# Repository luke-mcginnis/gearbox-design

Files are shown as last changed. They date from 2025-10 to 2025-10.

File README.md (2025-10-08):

# Gearbox Design Project

This was my final project for ME 330: Machine Design. The project goal was to design a three-stage gearbox using machine design principles including fatigue and failure analysis, material selection, bearing selection, and the AGMA design process. The end deliverables for this project were a [final report](/report.pdf) and gearbox powertrain CAD.

## [View final report](/report.pdf)
## [View final CAD](https://grabcad.com/library/three-stage-gearbox-2)

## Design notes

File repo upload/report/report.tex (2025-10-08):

\documentclass[titlepage]{article} % letter paper is implicit

\usepackage{siunitx} % for units
\usepackage{mathtools} % for amsmath
\usepackage{booktabs} % for better-looking tables
\usepackage{threeparttable} % for notes in tables
\usepackage[title]{appendix}
\usepackage{listings} % for source code
\usepackage{courier}
\usepackage[x11names]{xcolor} % for source code colors
\usepackage[moderate, % package to fit more text on a page, set moderate spacing
            mathspacing=normal, % keep horizontal spacing in math
            mathdisplays=normal, % keep vertical spacing around math
            leading=normal, % keep line spacing normal
            margins=tight, % allow custom margins (below)
            indent=normal,  % indent paragraphs normally
            marginwidth=1in]{savetrees} % set margin to 1in
\usepackage{biblatex} % For bibliography
\usepackage{amssymb} % For lists?
\usepackage{enumitem} % For lists?
\usepackage{tikz}  % FBDs with Plots
\usepackage{pgf} % Math printings
\usepackage{subcaption} % side by side figures
\usepackage{graphicx} % pictures
\usepackage{pdfpages} % drawings
% \setlength{\footskip}{30pt}

\sisetup{
    group-digits=integer,
    group-minimum-digits={3},
    group-separator={,},
    uncertainty-mode = separate,
    separate-uncertainty-units = single
}

\definecolor{codebackcolor}{rgb}{0.95,0.95,0.92}

\lstdefinestyle{myStyle}{
    backgroundcolor=\color{codebackcolor},   
    numberstyle=\tiny\color{gray},
    basicstyle=\ttfamily\footnotesize,
    identifierstyle=\color{Blue3},
    commentstyle=\color{SpringGreen4},
    keywordstyle=\color{Magenta3},
    stringstyle=\color{DarkOrange2},
    breakatwhitespace=false,         
    breaklines=true,                 
    keepspaces=true,                 
    numbers=left,       
    numbersep=5pt,                  
    showspaces=false,                
    showstringspaces=false,
    showtabs=false,                  
    tabsize=2,
}

\addbibresource{references.bib} % Import the bibliography file

\usetikzlibrary{backgrounds} % Plot Backgrounds
\usetikzlibrary{math} % Variables
\usetikzlibrary{patterns.meta} % cross hatch

\begin{document}

\title{Gearbox Design Report}
\author{Luke McGinnis\\Eastern Michigan University \\ME 330: Machine Design\\Dr. Emad Tanbour}

\date{April 21, 2025}

\maketitle

\tableofcontents

\begin{center}
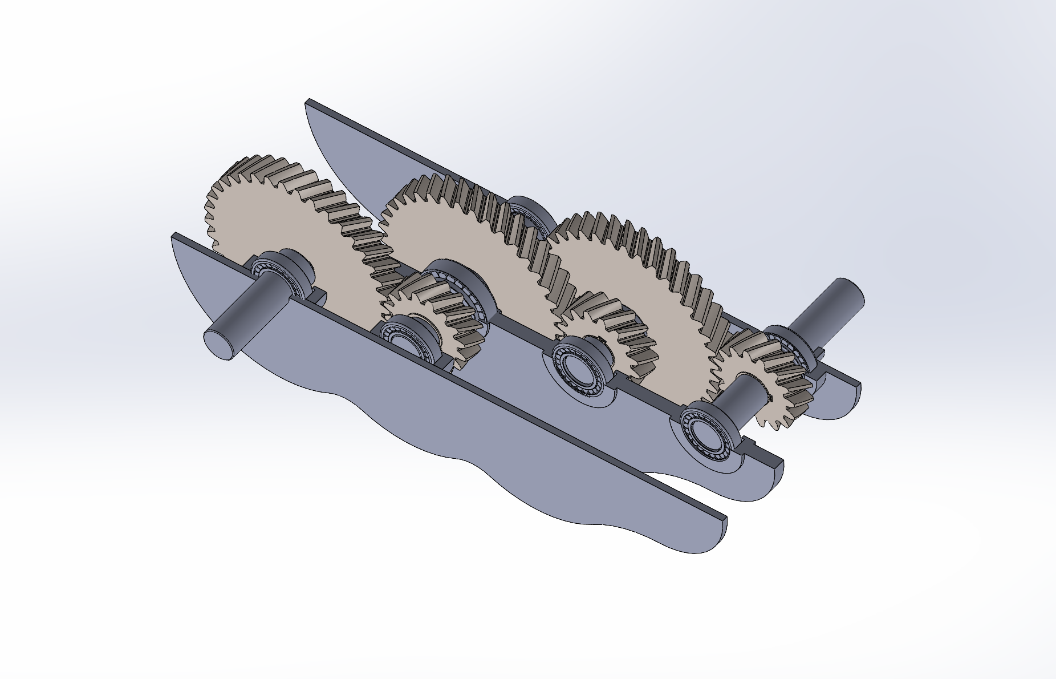
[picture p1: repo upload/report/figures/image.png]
    
\end{center}

\section{Introduction}

\subsection{Project Statement}
Using machine design principles, comprehensively design and create a CAD model
of a three-stage speed reduction gearbox. 

\subsection{Overall Requirements}
\begin{itemize}
    \item Reduce the shaft speed from an input of $\SI{1750}{rpm}$ to an output
    of $\SI{130(5)}{rpm}$.
    \item Tolerate an input power of $\SI{135}{hp}$.
    \item Consist of four shafts, one input, two intermediate, and one output.
    \item Use helical gears only.
    \item Be lubricated and sealed.
\end{itemize}

\subsection{Design Objectives}
\begin{itemize}
    \item Minimize the total size of the gearbox.
    \item Ensure the gearbox is easy to assemble and disassemble.
    \item Ensure manufacturability of all components.
\end{itemize}

\subsection{Methods}
\begin{itemize}
    \item Design report will be prepared with \LaTeX.
    \item CAD models, assemblies, drawing, simulations, and rendering will be
    prepared with Solidworks. 
\end{itemize}

\section{Gears Specifications}

\subsection{Requirements}
\begin{itemize}
    \item Overall gear train must convert $\SI{1750}{rpm}$ to $\SI{130(5)}{rpm}$.
    \item Gear train must handle an input power of $\SI{135}{hp}$.
    \item Gear train must be as compact as possible.
    \item All gears must be helical.
    \item Gears must be designed for a service life of \num{2000} hours per year
    and 6 years (\num{12000} hours total).
    \item Gears will be lubricated.
    \item AGMA (American Gear Manufacturers Association) design methodology will
    be used.
\end{itemize}

\subsection{Design Decisions}
\begin{itemize}
    \item All gears will use a standard pressure angle of \ang{20}. This is the
    most common pressure angle used for gearing and thus tooth cutters will be
    available for the greatest number of diametral pitches \cite{shigleydesign}.
    \item All gears will have full-depth teeth.
    \item All gears will have a helix angle of \ang{30}. This will allow for
    maximum advantage of strength and noise benefits of helical gears.
\end{itemize}

\subsection{Gear Ratio}
In order to achieve the smallest overall package size, we want our three stage 
ratios to be as close together as possible. Our requirements allow us to deviate
from our target output speed of \SI{130}{rpm} by as much as \SI{5}{rpm}. If we
assume the ideal case of all stage ratios being equal, we can calculate a target
individual stage ratio:

\begin{equation*}
    \frac{N_1}{N_2} = \frac{N_3}{N_4} = \frac{N_5}{N_6} = \sqrt[3]{\frac{13}{175}} \approx \frac{1}{2.379}
\end{equation*}

Now we can consider possible ratios that get close enough to this value by
limiting the denominator of this ideal ratio, to get the closest simple fraction
approximations.

\begin{table}[h]
    \centering
    \begin{threeparttable}
        \caption{Stage Gear Ratios Approximating a Ratio of 13:175}
        \vspace{0.25cm}
        \setlength{\tabcolsep}{10pt}
        \begin{tabular}{cccc}
            \toprule
            Stage Ratio & Train Value & Output Speed & Output Error \\
            $N_P:N_G$ & $e$ & $\omega_\textup{out}$ (rpm) & $\Delta\omega_\textup{out}$ (rpm) \\
            \midrule
            $37:88$ & 0.0743 & 130.1 & 0.075 \\
            $29:69$ & 0.0742 & 129.9 & 0.077 \\
            $21:50$ & 0.0741 & 129.7 & 0.35 \\
            $8:19$  & 0.0746 & 130.6 & 0.63 \\
            $5:12$  & 0.0723 & 126.6 & 3.4 \\
            $3:7$   & 0.0787 & 137.8 & 7.8 \\
            $2:5$   & 0.0640 & 112.0 & 18 \\
            \bottomrule
        \end{tabular}
        \label{tab:gear_ratios}
        \begin{tablenotes}
            \footnotesize
            \centering
            \item See Appendix \ref{sec:source_code} for generation source code used to
            generate this data.
        \end{tablenotes}
    \end{threeparttable}
\end{table}

From Table \ref{tab:gear_ratios}, we see that we have five ratios to choose from
that will produce a output speed within \SI{5}{rpm} of our target output speed
of \SI{130}{rpm}. We will choose a stage ratio of $8:19$ to get very close to
the target speed, and allow for scaling the ratio if we need to change our 
diametral pitch. Starting by doubling the values to $16:38$ and testing for 
meshing interference:

\begin{equation}
    N_{\textup{G, max}} = \frac{N_P^2 \sin^2(\phi_t) - 4k^2\cos^2(\psi)}{4k\cos(\psi)-2N_P\sin^2(\phi_t)} 
    = \frac{16^2 \sin^2(\ang{20}) - 4(1)\cos^2(\ang{30})}{4\cos(\ang{30})-2(16)\sin^2(\ang{20})} = -26.45 \tag*{(13-23) \cite{shigleydesign}}
\end{equation}

This means that there is no gear size of this specification that would interfere
with a pinion of 16 teeth, so we know there will not be any interference in the
gear train. We can now obtain our values for torque and speed:

\begin{table}[h!]
    \centering
    \caption{Transmission Values by Shaft}
    \vspace{0.25cm}
    \setlength{\tabcolsep}{15pt}
    \begin{tabular}{lcccc}
        \toprule
                         & \multicolumn{1}{c}{Input} & \multicolumn{2}{c}{Intermediate}& \multicolumn{1}{c}{Output}\\ 
                         \cmidrule(lr){2-2} \cmidrule(lr){3-4} \cmidrule(l){5-5}
        Shaft                     & A     &     B   &      C    &   D    \\
        \midrule
    Speed (\unit{rpm})            &  1750 &   736.8 &   310.2   &  130.6 \\
    Torque (\unit{lbf \cdot ft})  & 405.2 &   962.3 &   2285    &  5428  \\
    Pinion Tooth Count             &   16  &  16     &   16      &  --    \\ 
    Gear Tooth Count              & --    &  38     &   38      &   38   \\ 
    \bottomrule    
    \end{tabular}
\end{table}

For now, we can now proceed with tooth counts: 
$$\frac{N_P}{N_G} = \frac{N_1}{N_2} = \frac{N_3}{N_4} = \frac{N_5}{N_6} = \frac{16}{38}$$

\subsection{Estimation of Diametrical Pitch}

In order to reduce iteration, we will try to get a preliminary estimations of a
diametrical pitch for our gears. To do so, we will analyze the likely critical
gear in our gearbox, which is \#5, (pinion of shaft C) as it is the pinion
with the highest torque.

We will use equation 14-8 and rewrite it in terms of diametrical pitch $P$:
\begin{equation}
\sigma = \frac{K_{v} P W_{t}}{F Y} \implies P = \frac{F Y \sigma}{K_{v} W_{t}} \tag*{(14-8) \cite{shigleydesign}}
\end{equation}

\noindent We can simplify the gear to a spur gear, and use the following assumptions  \cite{shigleydesign}:

\begin{itemize}[label=]
    \item[$F$]: The face width is recommended to be $3p$ to $5p$.
    \item[$Y$]: The Lewis form factor ranges from $0.24$ to $0.485$.
    \item[$\sigma$]: Endurance strength of steel gears range from \SI{22}{ksi} to
    \SI{75}{ksi}.
    \item[$K_v$]: The velocity factor is a function of pitch-line velocity $V$,
    which is dependent on $P$. The velocity factor ranges from $\frac{600 +
    V}{600}$ to $\sqrt{\frac{78 + \sqrt{V}}{78}}$.
\end{itemize}

We can now rewrite all variables as constants or in terms of $P$ using $pP=\pi$,
$r=\frac{N}{2P}$, $V=\omega r$, and $W_t = \SI{135}{hp}/V$. 

After solving numerically, we can obtain a very conservative value of $P$ of
$\SI{1.891}{teeth/in}$, and a nonconservative value of $\SI{5.338}{teeth/in}$.
For now, we will choose from tooth sizes in general use \cite{shigleydesign},
and select $P_t=\SI{3}{teeth/in}$.

\section{Shaft Layout}
Our next step is specify  the general layout of the shafts and axial locations
of gears and bearings. In additon, we will address attaching components to
shafts.

\subsection{Requirements}
\begin{itemize}
    \item There must be 4 shafts: one input, two intermediate, and one output.
    \item Gearbox size must be minimized.
    \item Shafts should be as short as possible.
    \item Input and output shafts must extend outside of the gearbox housing by
    two times their diameter.
    \item Where possible, shaft diameters should be standard sizes.
    \item Shafts geometry should include means for rotating components to be
    affixed, such as keyways and retaining rings.
\end{itemize}

\subsection{Decisions}
\begin{itemize}
    \item In order to transmit torque via shafts, keyways will be used.
    \item Because helical gears will have a great axial force on one side, and
    little to no force on the other, a mix of shoulders and retaining rings will
    be used.
    \item Shoulders will be used to hold shafts in place on bearings.
\end{itemize}

\subsection{General Layout}

Based on these requirements and design decisions I designed a first iteration
of the shaft layout. My layout uses three planes of bearings and three planes of
gears to eliminate interference between gears. In this layout, shaft B is the
longest shaft, but is supported by three bearings, reducing the effective length.
This layout has one pair of gears above the middle bearing plane, and two pairs
below. I believe this is a flaw with this design: this causes shafts C and D to
have to be longer to accommodate the additonal gears and clearance. As shaft C or
D are likely critical due to the high torque on them, it is wise to adjust this
design to reduce the length of these shafts.

\begin{figure}[t]
    \centering
    \include{figures/rough_layout1.tex}
    \caption{First Iteration of General Gearbox Shaft Layout}
    \label{fig:layout1}
\end{figure}

I modified the layout to move an additional pair of gears above the middle plane of
bearings. This allowed me to reduce the length of shafts C and D by increasing
the lengths of A and B. This is reasonable, because it reduces the stress of the
most critical shafts, reducing the required diameter. Shaft C is now the longest
shaft, but again, the middle bearing significantly decreases the effective
length. 

\begin{figure}[t]
    \centering
    \include{figures/rough_layout2.tex}
    \caption{Final General Gearbox Shaft Layout}
    \label{fig:layout2}
\end{figure}

\subsection{Dimensions}

From the general layout, axial dimensions now have to be specified. Each shaft's
length is a combination of the following lengths:

\begin{itemize}[label=]
    \item[$F$] Face Width for helcial gears is recommended to be at least two
    times the axial pitch. Using formula (13-17)\cite{shigleydesign}, $p_x = p_t
    /2 \cdot \tan(\psi) = 2 \cdot \pi/3/\tan(\ang{30}) = 1.81$. Increase to \SI{2}{in} and
    revisit if needed.
    \item[$S$]: The axial length of the shoulder around the gear is determed by
    proportionality to the shaft minor diameter and shoulder diameter. This
    length will also accommodate the retaining hardware on the side of each gear
    opposite the axial force and shoulder. To meet both requirements, choose
    \SI{1}{in}.
    \item[$B$]: The axial length of the bearing is determined by the shortest
    bearing able to support the required load of each shaft. Estimate to be
    \SI{1}{in}.
    \item[$E$]: The external length of the input and output shafts from the
    gearbox housing. Per design requirements this must be double the diameter of
    the external shaft. As diameters are currently unknown, estimate to be
    \SI{2.5}{in}. This dimension will later accommodate shaft seals and likely
    need to be increased. but this portion of the shafts will just be under
    torsion and will not be critical, and therefore changes in $E$ will likely
    be inconsequential for stress life.
\end{itemize}

\subsection{Force Analysis}
Now that gear diameters and axial dimension are known we can produce free-body
diagrams, shear-moment diagrams, and obtain maximum bending moments for each
shaft.

\section{Shaft Design}

\subsection{Decisions}

\begin{itemize}
    \item Since all shafts must be designed for an infinite life, all shafts will
    be made of steel.
    \item To reduce costs and manufacturing difficulty, all shafts will be made
    of a single material.
\end{itemize}

\subsection{Force Analysis}

Due to the speed of the gearbox decreasing and the torque increasing, shaft C or
D are the critical shaft. I will conduct a force analysis on both to find the
most critical point. 

\textbf{Shaft C:}

\begin{equation*}
\begin{split}
    V_{34} &= \frac{\omega_C N_4}{P} = \SI{1029}{ft/min} \\
    W_{34}^t &= P/V_{34} = \SI{4330}{lbf} \\
    W_{34}^r &= W_{34}^t \tan(\phi_t) = \SI{1820}{lbf} \\
    W_{34}^x &= W_{34}^t \tan(\psi) = \SI{2500}{lbf} 
\end{split}
\hspace{0.5in}
\begin{split}
    V_{56} &= \frac{\omega_C N_5}{P} = \SI{433}{ft/min}\\
    W_{56}^t &= P/V_{56} = \SI{10284}{lbf} \\
    W_{56}^r &= W_{56}^t \tan(\phi_t) = \SI{-4322}{lbf} \\
    W_{56}^x &= W_{56}^t \tan(\psi) = \SI{-5937}{lbf} 
\end{split}
\end{equation*}

Shaft C has three bearings, two gears. Split shaft into two portions, left and
right and evaluate independently. The middle bearing will support the loads on both sides.

\begin{align*}
    \begin{split}
    R_{ay} &= -W^r_{34} \frac{B/2 + S + F/2}{l_{\text{left}}} = \SI{-569}{lbf} \\
    R_{by} &= -W^r_{34} \frac{B/2 + 2S + \frac{3}{2}F}{l_{\text{left}}} - \frac{1}{2}W^r_{56} = \SI{910}{lbf}\\
    R_{cy} &= -\frac{1}{2} W^r_{56} = \SI{2161}{lbf} \\
    \end{split}
    \quad
    \begin{split}
    R_{az} &= -W^t_{34} \frac{B/2 + S + F/2}{l_{\text{left}}} = \SI{-1351}{lbf} \\
    R_{bz} &= -W^t_{34} \frac{B/2 + 2S + \frac{3}{2}F}{l_{\text{left}}} - \frac{1}{2}W^t_{56} = \SI{-8119}{lbf} \\
    R_{cz} &= \frac{1}{2} W^t_{56} = \SI{-5142}{lbf} 
    \end{split}
\end{align*}

$$R_{bx} = \SI{-3438}{lbf} \quad T = \frac{W^t_{56} N_5}{2P} = \SI{27424}{lbf \cdot in} $$
\begin{figure}[h]
    \centering
    \include{figures/shaftC.tex}
    \caption{Force Analysis of Shaft C}
\end{figure}

\textbf{Shaft D:}

\begin{equation*}
\begin{split}
    W_{56}^t &= P/V_{56} = \SI{-9331}{lbf} \\
    W_{56}^r &= W_{56}^t \tan(\phi_t) = \SI{-3921}{lbf} \\
    W_{56}^x &= W_{56}^t \tan(\psi) = \SI{-5386}{lbf}
\end{split}
\hspace{0.5in}
\begin{split}
    R_y &= -\frac{1}{2}W_{56}^r = \SI{1960}{lbf} \\
    R_z &= -\frac{1}{2}W_{56}^t = \SI{4665}{lbf}
\end{split}
\end{equation*}

$$T = \frac{W^t_{56} N_6}{2P} = \SI{65133}{lbf \cdot in}$$

\begin{figure}[h!]
    \centering
    \include{figures/shaftD.tex}
    \caption{Force Analysis of Shaft D}
\end{figure}

\subsection{Stress Analysis}
Shafts C and D are both critical at the point of the meshing pair gears 5 and 6.
Both shafts have the same bending moment at that point, but shaft D has a far
higher torque. Therefore the axial location of gear 6 on shaft D is critical. 

First choose inexpensive 1020 CD Steel. Calculate endurance limit based off of
90\% reliability and a estimated \SI{2}{in} diameter:

\begin{equation*}
    S_e = k_a k_b k_e S_e' = 0.80 \cdot 0.82 \cdot 0.90 \cdot 0.5 \cdot \SI{68}{ksi} = \SI{19.9}{ksi}  \tag*{(6-17) \cite{shigleydesign}}
\end{equation*}

Using the DE-Goodman criteria, find the critical diameter for shaft D. This
location will have an end-milled keyway to transmit motion between gears, so
calculate fatigue notch factors \cite{shigleydesign}:

\begin{gather*} 
    r = 0.02 \cdot \SI{2}{in} = \SI{0.04}{in} \implies q = 0.65, q_s = 0.7 \\
    K_f = 1 + q\,(K_t - 1) = 1 + 0.65(2.14-1) = 1.74 \\
    K_{fs} = 1 + q_s(K_{ts} - 1) = 1 + 0.7(3.0-1) = 2.4
\end{gather*}
 
For a constantly rotating shaft, $T_a = M_m = 0$ and use values from force
analysis for $T_m$ and $M_a$. Also use $n=1.25$ for a factor of safety.

\begin{align*}
    A &= \sqrt{4 \cdot (K_f M_a)^2} = \sqrt{4 \cdot (1.74 \cdot 13944)^2} \\
    B &= \sqrt{3 \cdot (K_{fs} T_m)^2} = \sqrt{3 \cdot (2.4 \cdot 65133)^2}\\
    d & = \left[\frac{16}{n}\left(\frac{A}{S_e}+\frac{B}{S_{ut}}\right)\right]^{\frac{1}{3}} = \left[\frac{16}{1.25}\left(\frac{A}{19.9}+\frac{B}{68}\right)\right]^{\frac{1}{3}} = \SI{3.44}{in} \tag*{(7-7) \cite{shigleydesign}}
\end{align*}

This is higher than I wanted the diameter to be due to having to increase it
further for shoulders and bearing, and in order to make the gearbox profile size
smaller, I will upgrade the material to Ground 4140 Q\&T Steel. Now using $S_{ut}
= \SI{225}{ksi}$, $k_a =  1.21 \cdot 225^{-0.067} = 0.84$, and $S_e =
\SI{61.6}{ksi}$.

$$d = \left[\frac{16}{1.25}\left(\frac{A}{61.6}+\frac{B}{225}\right)\right]^{\frac{1}{3}} = \SI{2.33}{in}$$

\noindent Increase this to \SI{2.5}{in}. This diameter will be the minimum
diameter of all shafts in the gearbox. Next check first cycle yielding by
checking critical point of shaft D:

\begin{align*}
    \sigma'_\textup{max} &= \left[\left(\frac{32 K_f M_a}{\pi d^3}\right)^2 + 3 \left(\frac{16 K_{fs} T_m}{\pi d^3}\right) \right]^\frac{1}{2}\\
                         &= \left[\left(\frac{32 \cdot 2.4 \cdot 13944}{\pi \cdot 2.5^3}\right)^2 + 3 \left(\frac{16 \cdot 2.4 \cdot 65133}{\pi \cdot 2.5^3}\right) \right]^\frac{1}{2}\\
                         &= \SI{112.3}{ksi} \\
    n_y &= \frac{S_y}{\sigma'_\textup{max}} = \frac{208}{90.9} = 2.29
\end{align*}

Next check sensitive points for deflection and slope. One option would be to use beam deflection equations, but I chose to use the 
derivative relationship between bending moment, slope, and deflection:

\begin{gather*}
    \theta(x) = \frac{1}{EI}\int{Mdx} \\
    y(x) = \int{\theta(x)} = \frac{1}{EI}\int{\int{Mdx} dx} \\
    E = \SI{30000}{ksi} \quad I = \frac{\pi(\SI{2.5}{in})^4}{64}
\end{gather*}

\begin{table}[h]
    \centering
    \begin{threeparttable}
        \caption{Slope and Deflection Values along Shaft C}
        \vspace{0.25cm}
        
        \begin{tabular}{lccc}
            \toprule
            Point of Interest & Position  & Slope  & Deflection\\
              & $x$ (\unit{in}) & $\theta$ \unit{rad} & y (\unit{in})\\
            \midrule
            Left Bearing   & 0.5  & 0.0000032 &  0.00000053\\
            Gear 4         & 5.5  & 0.00039 & 0.00071\\
            Middle Bearing & 8    & 0.00056 & 0.0020 \\
            Gear 5         & 10.5 & 0.00086 & 0.0036\\
            Right Bearing  & 13   & 0.0012 & 0.0063 \\
            \bottomrule
        \end{tabular}
        \label{tab:shaftCdeflect}
    \end{threeparttable}
\end{table}

All bearings and gears are within the required limits, although the right
bearing slope is just barley within limits\cite{shigleydesign}. Consider during bearing selection.

\section{Gears}

Continuing with perviously used specification for gears and loading, I now need
to fully specify gears. Since gear 5 is the smallest gear transmitting the
largest load, it will be critical.

\textbf{Gear 5 Wear:}

\begin{gather*}
    I = \frac{\cos{\phi_t}\sin{\phi_t}m_G}{2m_N (m_G-1)} = \frac{\cos{(\ang{22.80})}\sin{(\ang{22.80})}\frac{38}{16}}{2\cdot1 (\frac{38}{16} - 1)} = 0.31\\
    Q_v = 7, B = 0.731, A = 65.1\\
    K_v = \left(\frac{A+\sqrt{V_5}}{A}\right)^B =  1.22\\
    K_m = 1.21\\
    C_p = 2300\\
    K_o = K_s = C_f = 1\\
    \sigma_c = C_p \sqrt{W_t K_o K_v K_s \frac{K_m C_f}{d_p F I}} = \SI{148446}{psi}
\end{gather*}

For life factor $Z_N$ get number of cycles for specified life of \SI{12000}{hours}.
\begin{gather*}
    L_4 = \SI{12000}{hours} \cdot \SI{310}{rpm} = 2.23 \times 10^8 \unit{rev}\\
    Z_N = 0.95, K_R = K_T = C_H = 1, S_H=1.1\\
    S_c = \frac{S_H \sigma_c}{Z_N} = \frac{1.1 \cdot 148446}{0.95} = \SI{171885}{psi}
\end{gather*}
Select grade 2 carburized and hardened steel with $S_c = \SI{225000}{psi}$. $n_c
= 225000 \cdot 0.9 / 197928 = 1.18$.

\textbf{Gear 5 Bending:}
\begin{gather*}
    J=0.40, K_B = 1\\
    \sigma = W_t K_v \frac{P_d K_m}{F J} = \SI{51654}{psi}\\
    Y_N = 0.95\\
    \sigma_{\textup{allow}} = S_t Y_N = \SI{58500}{psi}\\
    n=\frac{58500}{51654} = 1.13
\end{gather*}

\section{Other Components}
\subsection{Bearings}
Tapered roller bearings must be used to allow for axial loads due to the helical
gears. These bearings should be able to be housed by the gearbox casting. The
greatest axial force is from gear 6 pushing onto the outer bearing of shaft D at
\SI{5938}{lbf}. The greatest radial force is on both bearings of shaft D with a
value of \SI{2161}{lbf}. This is a combined load of \SI{6318}{lbf}.

Using the supplier SXF's catalog to find bearings with a bore diameter of
\SI{2.5}{in}, and with load limits above those required, I selected part number
39585/39520 \cite{sxfbearing}. This bearing is also compatible with the required
speeds, cycles, and mounting requirements. Additionally, bearing 663/653 will be
used for the center of shaft C in order to accommodate a larger shaft diameter.

\subsection{Lubrication}
For helical gears with continuous duty and pitch line velocity over
\SI{1000}{ft/min}, select AGMA 6 EP.

\subsection{Keys}
Standard \SI{0.5}{in} square keys will be used. Using same  4140 Q\&T Steel,
check for failure by crushing:
\begin{gather*}
    F = \frac{T}{r} = \frac{65133}{2.5} = \SI{26053}{lbf}\\
    l = \frac{2 F n}{t S_y} = \frac{2 \cdot 26053 \cdot n}{0.5 \cdot 225000} = \SI{0.93}{in} \SI{1}{in}
\end{gather*}

\subsection{Other Considerations}
\begin{itemize}
    \item Gearbox housing
    \item Gearbox mounting
    \item Lubrication
    \item Sealing
    \item Maintenance/Inspection Schedule
    \item FMEA 
\end{itemize}

\newpage
\section{Appendices}

\begin{appendices}

    \section{Source Code}
    \label{sec:source_code}

    \lstinputlisting[ title={Script Used to Generate Possible Gear Ratios
        \footnotesize{(\texttt{approximate\_gear\_ratio.py})}}, language=Python,
        style=myStyle, ]{../scripts/approximate_gear_ratio.py}

\section{Drawings}
\includepdf[fitpaper=true, pages=-]{../cad/drawings/ShaftA.pdf}
\includepdf[fitpaper=true, pages=-]{../cad/drawings/ShaftB.pdf}
\includepdf[fitpaper=true, pages=-]{../cad/drawings/ShaftC.pdf}
\includepdf[fitpaper=true, pages=-]{../cad/drawings/ShaftD.pdf}

\end{appendices}

\printbibliography

\end{document}

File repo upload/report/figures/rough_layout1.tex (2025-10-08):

\tikzmath{
    \fa = 1;
    \sh = 1;
    \be = 1;
    \ex = 2;
    \startx = 3;
    \starty = 16;
    \diameterP = 2;
    \diameterG = 5;
    \lefthand = -30;
    \righthand = \lefthand * -1;
    \centerdist = (\diameterP+\diameterG)/2;
}

\newcommand{\Gear}[5] % x, y, d, face, angle
{
    \draw[thick, fill=white] (#1 - #3/2, #2) rectangle (#1 + #3/2, #2 + #4);
    \draw[thick, pattern={Lines[angle=90-#5,distance=3pt,line width=0.5pt]}] (#1 - #3/2, #2) rectangle (#1 + #3/2, #2 + #4);
    
}

\newcommand{\Bearing}[4] % x, y, width, height
{
    \draw (#1, #2) rectangle (#1+#3, #2+#4);
    \draw (#1, #2) -- (#1+#3, #2+#4);
    \draw (#1, #2+#4) -- (#1+#3, #2);
}

\begin{tikzpicture}[scale=0.7, x=0.25in, y=0.25in, show background rectangle, inner frame xsep=50pt]
    \draw[fill=gray!15] (\startx-1,\starty-\ex) rectangle (17, 3);

    % \draw[help lines, step=0.25in] (0,0) grid (24, 17); % TEMP HELPER GRID
    \draw[thick, fill=gray!30] (\startx,\starty) rectangle (\startx+1, \starty-\ex-2*\be-2*\sh-\fa);
    \draw[dash pattern=on 2pt off 3pt on 8pt off 3pt] (\startx+0.5,\starty+0.5) node [above] {$A$} -- (\startx+0.5, \starty-\ex-2*\be-2*\sh-\fa-0.5) node [below] {$A$};
    \Bearing{\startx}{\starty-\ex-\be}{1}{1}
    \Bearing{\startx}{\starty-\ex-\fa-\sh-\sh-\be-\be}{1}{1}
    \Gear{\startx+.5}{\starty-\ex-\sh-\be-\fa}{\diameterP}{\fa}{\righthand}

    \draw[thick, fill=gray!30] (\startx+\centerdist,\starty-\ex)
     rectangle (\startx+1+\centerdist, \starty-\ex-3*\be-5*\sh-3*\fa);
    \draw[dash pattern=on 2pt off 3pt on 8pt off 3pt] (\startx+\centerdist+0.5,\starty-\ex+0.5) node [above] {$B$} -- (\startx+0.5+\centerdist, \starty-\ex-3*\be-5*\sh-3*\fa-0.5) node [below] {$B$};
    \Bearing{\startx+\centerdist}{\starty-\ex-\be}{1}{1}
    \Bearing{\startx+\centerdist}{\starty-\ex-\fa-\sh-\sh-\be-\be}{1}{1}
    \Bearing{\startx+\centerdist}{\starty-\ex-3*\be-5*\sh-3*\fa}{1}{1}
    \Gear{\startx+\centerdist+.5}{\starty-\ex-\sh-\be-\fa}{\diameterG}{\fa}{\lefthand}
    \Gear{\startx+\centerdist+.5}{\starty-\ex-2*\be-3*\sh-2*\fa}{\diameterP}{\fa}{\righthand}

    \draw[thick, fill=gray!30] (\startx+2*\centerdist,\starty-\ex-\sh*2-\fa-\be)
     rectangle (\startx+1+2*\centerdist, \starty-\ex-3*\be-5*\sh-3*\fa);
    \draw[dash pattern=on 2pt off 3pt on 8pt off 3pt] (\startx+2*\centerdist+0.5,\starty-\ex-\sh*2-\fa-\be+0.5) node [above] {$C$} -- (\startx+2*\centerdist+0.5, \starty-\ex-3*\be-5*\sh-3*\fa-0.5) node [below] {$C$};
    \Bearing{\startx+2*\centerdist}{\starty-\ex-\fa-\sh-\sh-\be-\be}{1}{1}
    \Bearing{\startx+2*\centerdist}{\starty-\ex-3*\be-5*\sh-3*\fa}{1}{1}
    \Gear{\startx+2*\centerdist+.5}{\starty-\ex-2*\be-3*\sh-2*\fa}{\diameterG}{\fa}{\lefthand}
    \Gear{\startx+2*\centerdist+.5}{\starty-\ex-2*\be-4*\sh-3*\fa}{\diameterP}{\fa}{\righthand}

    \draw[thick, fill=gray!30] (\startx+3*\centerdist,\starty-\ex-\sh*2-\fa-\be)
     rectangle (\startx+1+3*\centerdist, \starty-\ex-3*\be-5*\sh-3*\fa-\ex);
     \draw[dash pattern=on 2pt off 3pt on 8pt off 3pt]  (\startx+3*\centerdist+0.5,\starty-\ex-\sh*2-\fa-\be+0.5) node [above] {$D$} -- (\startx+3*\centerdist+0.5, \starty-\ex-3*\be-5*\sh-3*\fa-\ex-0.5) node [below] {$D$};
    \Bearing{\startx+3*\centerdist}{\starty-\ex-\fa-\sh-\sh-\be-\be}{1}{1}
    \Bearing{\startx+3*\centerdist}{\starty-\ex-3*\be-5*\sh-3*\fa}{1}{1}
    \Gear{\startx+3*\centerdist+.5}{\starty-\ex-2*\be-4*\sh-3*\fa}{\diameterG}{\fa}{\lefthand}

\end{tikzpicture}

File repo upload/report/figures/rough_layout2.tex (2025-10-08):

\tikzmath{
    \fa = 1;
    \sh = 1;
    \be = 1;
    \ex = 2;
    \startx = 3;
    \starty = 16;
    \diameterP = 2;
    \diameterG = 5;
    \lefthand = -30;
    \righthand = \lefthand * -1;
    \centerdist = (\diameterP+\diameterG)/2;
}

\newcommand{\Gear}[5] % x, y, d, face, angle
{
    \draw[thick, fill=white] (#1 - #3/2, #2) rectangle (#1 + #3/2, #2 + #4);
    \draw[thick, pattern={Lines[angle=90-#5,distance=3pt,line width=0.5pt]}] (#1 - #3/2, #2) rectangle (#1 + #3/2, #2 + #4);
    
}

\newcommand{\Bearing}[4] % x, y, width, height
{
    \draw (#1, #2) rectangle (#1+#3, #2+#4);
    \draw (#1, #2) -- (#1+#3, #2+#4);
    \draw (#1, #2+#4) -- (#1+#3, #2);
}

\begin{tikzpicture}[scale=0.7, x=0.25in, y=0.25in, show background rectangle, inner frame xsep=50pt]
    \draw[fill=gray!15] (\startx-1,\starty-\ex) rectangle (17, 3);

    % \draw[help lines, step=0.25in] (0,0) grid (24, 17); % TEMP HELPER GRID
    \draw[thick, fill=gray!30] (\startx,\starty) rectangle (\startx+1, \starty-\ex-2*\be-3*\sh-2*\fa);
    \draw[dash pattern=on 2pt off 3pt on 8pt off 3pt] (\startx+0.5,\starty+0.5) node [above] {$A$} -- (\startx+0.5, \starty-\ex-2*\be-3*\sh-2*\fa-0.5) node [below] {$A$};
    \Bearing{\startx}{\starty-\ex-\be}{1}{1}
    \Bearing{\startx}{\starty-\ex-2*\fa-3*\sh-\be-\be}{1}{1}
    \Gear{\startx+.5}{\starty-\ex-\sh-\be-\fa}{\diameterP}{\fa}{\righthand}

    \draw[thick, fill=gray!30] (\startx+\centerdist,\starty-\ex)
     rectangle (\startx+1+\centerdist, \starty-\ex-2*\be-3*\sh-2*\fa);
    \draw[dash pattern=on 2pt off 3pt on 8pt off 3pt] (\startx+\centerdist+0.5,\starty-\ex+0.5) node [above] {$B$} -- (\startx+0.5+\centerdist, \starty-\ex-2*\be-3*\sh-2*\fa-0.5) node [below] {$B$};
    \Bearing{\startx+\centerdist}{\starty-\ex-\be}{1}{1}
    \Bearing{\startx+\centerdist}{\starty-\ex-2*\fa-3*\sh-\be-\be}{1}{1}
    \Gear{\startx+\centerdist+.5}{\starty-\ex-\sh-\be-\fa}{\diameterG}{\fa}{\lefthand}
    \Gear{\startx+\centerdist+.5}{\starty-\ex-2*\sh-\be-2*\fa}{\diameterP}{\fa}{\righthand}

    \draw[thick, fill=gray!30] (\startx+2*\centerdist,\starty-\ex)
     rectangle (\startx+1+2*\centerdist, \starty-\ex-3*\be-5*\sh-3*\fa);
    \draw[dash pattern=on 2pt off 3pt on 8pt off 3pt] (\startx+2*\centerdist+0.5,\starty-\ex+0.5) node [above] {$C$} -- (\startx+2*\centerdist+0.5, \starty-\ex-3*\be-5*\sh-3*\fa-0.5) node [below] {$C$};
    \Bearing{\startx+2*\centerdist}{\starty-\ex-\be}{1}{1}
    \Bearing{\startx+2*\centerdist}{\starty-\ex-2*\be-3*\sh-2*\fa}{1}{1}
    \Bearing{\startx+2*\centerdist}{\starty-\ex-3*\be-5*\sh-3*\fa}{1}{1}
    \Gear{\startx+2*\centerdist+.5}{\starty-\ex-\fa-\sh-\sh-\be-\be}{\diameterG}{\fa}{\lefthand}
    \Gear{\startx+2*\centerdist+.5}{\starty-\ex-2*\be-4*\sh-3*\fa}{\diameterP}{\fa}{\righthand}

    \draw[thick, fill=gray!30] (\startx+3*\centerdist, \starty-\ex-1*\be-3*\sh-2*\fa)
     rectangle (\startx+1+3*\centerdist, \starty-\ex-3*\be-5*\sh-3*\fa-\ex);
     \draw[dash pattern=on 2pt off 3pt on 8pt off 3pt]  (\startx+3*\centerdist+0.5,\starty-\ex-1*\be-3*\sh-2*\fa+0.5) node [above] {$D$} -- (\startx+3*\centerdist+0.5, \starty-\ex-3*\be-5*\sh-3*\fa-\ex-0.5) node [below] {$D$};
    \Bearing{\startx+3*\centerdist}{\starty-\ex-2*\be-3*\sh-2*\fa}{1}{1}
    \Bearing{\startx+3*\centerdist}{\starty-\ex-3*\be-5*\sh-3*\fa}{1}{1}
    \Gear{\startx+3*\centerdist+.5}{\starty-\ex-2*\be-4*\sh-3*\fa}{\diameterG}{\fa}{\lefthand}

\end{tikzpicture}

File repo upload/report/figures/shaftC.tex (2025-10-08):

\tikzmath{
  \startx = 1.5;
  \coloff = 12;
  \shafty = 18.5;
  \sheary = 12.5;
  \momenty = 6.5;
  \torquey = 0;
  \beamlen = 9;
  \xs = 8/13;
  \x0 = \startx + 0.5;
  \x1 = \startx + 5.5*\xs;
  \x2 = \startx + 8*\xs;
  \x3 = \startx + 11*\xs;
  \x4 = \startx + 13*\xs + 0.5;
  \forceyone = 4000;
  \forceytwo = 3000;
  \shearyval1 = 2;
  \shearyval2 = 1.5;
  \momentyval1 = -3128/3000;
  \momentyval2 = 0;
  \momentyval3 = 5408/3000;
  \forcezone = 3500;
  \forceztwo = 2500;
  \shearzval1 = -1353/2000;
  \shearzval2 = 2977/2000;
  \momentzval1 = -1;
  \momentzval2 = 0;
  \momentzval3 = -2;
}

\begin{tikzpicture}[x=0.25in, y=0.25in, background rectangle/.style={fill=cyan!10}, show background rectangle]
    % \draw[help lines, step=0.25in] (0,0) grid (24, 24); % TEMP HELPER GRID

    % === FORCE DIAGRAM - Y COLUMN ===
    \draw[thick, fill=white] (\startx,\shafty) rectangle (\startx+\beamlen,\shafty+1);
    \draw[dash pattern=on 2pt off 3pt on 8pt off 3pt] (\startx - 0.5, \shafty + 0.5) -- (\startx + \beamlen + 0.5, \shafty + 0.5) node [right] {$x$};
    \draw (\x0, \shafty + 1.125) -- (\x0, \shafty + 3) node [above] {$y$};

    % Left support
    \draw (\startx, \shafty) -- (\startx+1, \shafty+1);
    \draw (\startx, \shafty+1) -- (\startx+1, \shafty);
    \draw (\startx+1, \shafty) -- (\startx+1, \shafty+1);

    % Right support
    \draw (\startx+\beamlen-1, \shafty) -- (\startx+\beamlen, \shafty+1);
    \draw (\startx+\beamlen-1, \shafty+1) -- (\startx+\beamlen, \shafty);
    \draw (\startx+\beamlen-1, \shafty) -- (\startx+\beamlen-1, \shafty+1);

    % Middle support
    \draw (\x2-0.5, \shafty) -- (\x2+0.5, \shafty+1);
    \draw (\x2-0.5, \shafty) -- (\x2-0.5, \shafty+1);
    \draw (\x2-0.5, \shafty+1) -- (\x2+0.5, \shafty);
    \draw (\x2-0.5, \shafty) -- (\x2+0.5, \shafty+1);
    \draw (\x2+0.5, \shafty) -- (\x2+0.5, \shafty+1);

    % Reactions
    \draw[ultra thick, stealth-] (\x0, \shafty+1) -- (\x0, \shafty+2) node[right] {$R_{ay}$};
    \draw[ultra thick, stealth-] (\x2, \shafty) -- (\x2, \shafty-1.1) node[below] {$R_{by}$};

    \draw[ultra thick, stealth-] (\x4, \shafty) -- (\x4, \shafty-1.5) node[below] {$R_{cy}$};

    % Loads
    \draw[ultra thick, stealth-] (\x1, \shafty) -- (\x1, \shafty-1.5) node[below] {$W_{34}^r$};
    \draw[ultra thick, stealth-] (\x3, \shafty+1) -- (\x3, \shafty+3) node[above] {$W_{56}^r$};

    % % Dimensions
    % \draw[thick, stealth-stealth] (\x0 + 1/36, \shafty-0.5) -- (\x1 - 1/36, \shafty-0.5) node [midway, fill=cyan!10] {1};
    % \draw (\x1, \shafty - 0.625) -- (\x1, \shafty - 0.125);

    % \draw[thick, stealth-stealth] (\x0 + 1/36, \shafty - 1.0) -- (\x2 - 1/36, \shafty - 1.0) node [midway, fill=cyan!10] {2};
    % \draw (\x2, \shafty - 1.125) -- (\x2, \shafty - 0.125);

    % \draw[thick, stealth-stealth] (\x0 + 1/36, \shafty - 1.5) -- (\x3 - 1/36, \shafty - 1.5) node [midway, fill=cyan!10] {3};

    % === SHEAR - Y ===
    \draw[fill=white] (\x0, \sheary) rectangle (\x1, \sheary-0.53);
    \fill[fill=white] (\x1, \sheary) rectangle (\x2, \sheary-0.53+1.7);
    \fill[fill=white] (\x2, \sheary) rectangle (\x3, \sheary-0.53+1.7+0.84);
    \fill[fill=white] (\x3, \sheary) rectangle (\x4, \sheary-0.53+1.7+0.84-4);
    \draw (\x0, \sheary) node [left] {$O$} -- (\x0 + \beamlen, \sheary) node [right] {$x$};
    \draw (\x0, \sheary+2.5) node [left] {$V_{xz} (\unit{lbf})$} -- (\x0, \sheary-2.5);

    \draw[very thick] 
        (\x0, \sheary) -- 
        (\x0, \sheary-0.53) -- 
        (\x1, \sheary-0.53) node[midway, below] {$-569$} -- 
        (\x1, \sheary-0.53+1.7) -- 
        (\x2, \sheary-0.53+1.7) node[midway, above] {$1255$} -- 
        (\x2, \sheary-0.53+1.7+0.84) -- 
        (\x3, \sheary-0.53+1.7+0.84) node[midway, above] {$2161$} -- 
        (\x3, \sheary-0.53+1.7+0.84-4) -- 
        (\x4, \sheary-0.53+1.7+0.84-4) node[midway, below] {$2161$} -- 
        (\x4, \sheary);

    % === MOMENT - Y ===
    \fill[white] (\x0, \momenty) -- 
        (\x1, \momenty+\momentyval1) -- 
        (\x2, \momenty+\momentyval2) -- 
        (\x3, \momenty+\momentyval3) -- 
        (\x4, \momenty) -- cycle;
    \draw (\x0, \momenty) node [left] {$O$} -- (\x0 + \beamlen, \momenty) node [right] {$x$};
    \draw (\x0, \momenty+2.5) node [align=center, left] {$M_{xz}$\\$(\unit{lbf\cdot in})$} -- (\x0, \momenty-2.5);
    \draw[very thick] 
        (\x0, \momenty) -- 
        (\x1, \momenty+\momentyval1) node [below] {$-3128$} -- 
        (\x2, \momenty+\momentyval2) -- 
        (\x3, \momenty+\momentyval3) node [above] {$5408$} -- 
        (\x4, \momenty);

    % === TORSION ===
    \draw (\x0, \torquey) node [left] {$O$} -- (\x0 + \beamlen, \torquey) node [right] {$x$};
    \draw (\x0, \torquey+2.5) node [align=center, left] {$T$\\$(\unit{lbf\cdot in})$} -- (\x0, \torquey);
    \draw[fill=white] (\x1, \torquey) rectangle (\x3, \torquey+\shearyval2);
    \draw[very thick] 
        (\x0, \torquey) -- 
        (\x1, \torquey) -- 
        (\x1, \torquey+\shearyval2) -- 
        (\x3, \torquey+\shearyval2) node[midway, above] {$27424$} -- 
        (\x3, \torquey+\shearyval2)  -- 
        (\x3, \torquey) --
        (\x4, \torquey);

    % === FORCE DIAGRAM - Z COLUMN ===
    \draw[thick, fill=white] (\startx + \coloff, \shafty) rectangle (\startx + \beamlen + \coloff, \shafty + 1);
    \draw[dash pattern=on 2pt off 3pt on 8pt off 3pt] (\startx - 0.5 + \coloff, \shafty + 0.5) -- (\startx + \beamlen + 0.5 + \coloff, \shafty + 0.5) node [right] {$x$};
    \draw (\x0 + \coloff, \shafty + 1.125) -- (\x0 + \coloff, \shafty + 3) node [above] {$z$};

    % Supports
    \draw (\startx + \coloff, \shafty) -- (\startx + 1 + \coloff, \shafty + 1);
    \draw (\startx + \coloff, \shafty + 1) -- (\startx + 1 + \coloff, \shafty);
    \draw (\startx + 1 + \coloff, \shafty) -- (\startx + 1 + \coloff, \shafty + 1);
    \draw (\startx + \beamlen - 1 + \coloff, \shafty) -- (\startx + \beamlen + \coloff, \shafty + 1);
    \draw (\startx + \beamlen - 1 + \coloff, \shafty + 1) -- (\startx + \beamlen + \coloff, \shafty);
    \draw (\startx + \beamlen - 1 + \coloff, \shafty) -- (\startx + \beamlen - 1 + \coloff, \shafty + 1);

    % Middle support
    \draw (\x2-0.5 + \coloff, \shafty) -- (\x2+0.5+ \coloff, \shafty+1);
    \draw (\x2-0.5 + \coloff, \shafty) -- (\x2-0.5+ \coloff, \shafty+1);
    \draw (\x2-0.5 + \coloff, \shafty+1) -- (\x2+0.5+ \coloff, \shafty);
    \draw (\x2-0.5 + \coloff, \shafty) -- (\x2+0.5+ \coloff, \shafty+1);
    \draw (\x2+0.5 + \coloff, \shafty) -- (\x2+0.5+ \coloff, \shafty+1);

    % Reactions
    \draw[ultra thick, stealth-] (\x0 + \coloff, \shafty+1) -- (\x0 + \coloff, \shafty+2) node[right] {$R_{az}$};
    \draw[ultra thick, stealth-] (\x2 + \coloff, \shafty+1) -- (\x2 + \coloff, \shafty+2.3) node[above] {$R_{bz}$};
    \draw[ultra thick, stealth-] (\x4 + \coloff, \shafty+1) -- (\x4 + \coloff, \shafty+2.2) node[above] {$R_{cz}$};

    % Loads
    \draw[ultra thick, stealth-] (\x1 + \coloff, \shafty) -- (\x1 + \coloff, \shafty-1) node[below] {$W_{34}^t$};
    \draw[ultra thick, stealth-] (\x3 + \coloff, \shafty) -- (\x3 + \coloff, \shafty-1.75) node[below] {$W_{56}^t$};

    % Dimensions - Z column
    % \draw[thick, stealth-stealth] (\x0 + \coloff + 1/36, \shafty - 0.5) -- (\x1 + \coloff - 1/36, \shafty - 0.5) node [midway, fill=cyan!10] {1};
    % \draw (\x1 + \coloff, \shafty - 0.625) -- (\x1 + \coloff, \shafty - 0.125);

    % \draw[thick, stealth-stealth] (\x0 + \coloff + 1/36, \shafty - 1.0) -- (\x2 + \coloff - 1/36, \shafty - 1.0) node [midway, fill=cyan!10] {2};
    % \draw (\x2 + \coloff, \shafty - 1.125) -- (\x2 + \coloff, \shafty - 0.125);

    % \draw[thick, stealth-stealth] (\x0 + \coloff + 1/36, \shafty - 1.5) -- (\x3 + \coloff - 1/36, \shafty - 1.5) node [midway, fill=cyan!10] {3};

    % === SHEAR - Z ===
    \draw (\x0 + \coloff, \sheary) node [left] {$O$} -- (\x0 + \beamlen + \coloff, \sheary) node [right] {$x$};
    \draw (\x0 + \coloff, \sheary+2.5) node [left] {$V_{xy} (\unit{lbf})$} -- (\x0 + \coloff, \sheary - 2.5);
    \draw[fill=white] (\x0 + \coloff, \sheary) rectangle (\x1 + \coloff, \sheary+\shearzval1);
    \draw[fill=white] (\x1 + \coloff, \sheary) rectangle (\x2 + \coloff, \sheary+\shearzval2);
    \draw[fill=white] (\x2 + \coloff, \sheary) rectangle (\x3 + \coloff, \sheary-5/2);
    \draw[fill=white] (\x3 + \coloff, \sheary) rectangle (\x4 + \coloff, \sheary+5/2);
    \draw[very thick]
        (\x0 + \coloff, \sheary) --
        (\x0 + \coloff, \sheary+\shearzval1) --
        (\x1 + \coloff, \sheary+\shearzval1) node[midway, below] {$-1353$} --
        (\x1 + \coloff, \sheary+\shearzval2) --
        (\x2 + \coloff, \sheary+\shearzval2) node[midway, above] {$2977$} --
        (\x2 + \coloff, \sheary-5/2) --
        (\x3 + \coloff, \sheary-5/2) node[midway, below] {$-5142$}--
        (\x3 + \coloff, \sheary+5/2) --
        (\x4 + \coloff, \sheary+5/2) node[midway, above] {$5142$} --
        (\x4 + \coloff, \sheary);

    % === MOMENT - Z ===
    \fill[white] (\x0 + \coloff, \momenty) --
        (\x1 + \coloff, \momenty+\momentzval1) --
        (\x2 + \coloff, \momenty+\momentzval2) --
        (\x3 + \coloff, \momenty) -- cycle;
    \fill[white] (\x2 + \coloff, \momenty) --
        (\x3 + \coloff, \momenty+\momentzval3) --
        (\x4 + \coloff, \momenty+\momentzval2) -- cycle;
    \draw (\x0 + \coloff, \momenty) node [left] {$O$} -- (\x0 + \beamlen + \coloff, \momenty) node [right] {$x$};
    \draw (\x0 + \coloff, \momenty+2.5) node [align=center, left] {$M_{xy}$\\$(\unit{lbf\cdot in})$} -- (\x0 + \coloff, \momenty-2.5);
    \draw[very thick]
        (\x0 + \coloff, \momenty) --
        (\x1 + \coloff, \momenty+\momentzval1) node[below] {$-7442$} --
        (\x2 + \coloff, \momenty+\momentzval2) --
        (\x3 + \coloff, \momenty+\momentzval3) node[below] {$-12855$}--
        (\x4 + \coloff, \momenty);

    % === MOMENT - COMB ===
    \fill[white] (\x0 + \coloff, \torquey) --
        (\x1 + \coloff, \torquey+1.3) --
        (\x2 + \coloff, \torquey) --
        (\x3 + \coloff, \torquey + 2.25) --
        (\x4 + \coloff, \torquey) -- cycle;
    \draw (\x0 + \coloff, \torquey) node [left] {$O$} -- (\x0 + \beamlen + \coloff, \torquey) node [right] {$x$};
    \draw (\x0 + \coloff, \torquey+2.5) node [align=center, left] {$M_{total}$\\$(\unit{lbf\cdot in})$} -- (\x0 + \coloff, \torquey);
    \draw[very thick]
        (\x0 + \coloff, \torquey) --
        (\x1 + \coloff, \torquey+1.3) node[above] {$8072$} --
        (\x2 + \coloff, \torquey) --
        (\x3 + \coloff, \torquey+2.25) node[above] {$13944$} --
        (\x4 + \coloff, \torquey);
\end{tikzpicture}

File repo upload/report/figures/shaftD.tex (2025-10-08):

\tikzmath{
  \startx = 1.5;
  \coloff = 12;
  \shafty = 18.5;
  \sheary = 12.5;
  \momenty = 6.5;
  \torquey = 0;
  \beamlen = 9;
  \x0 = \startx + 0.5;
  \x1 = \startx + \beamlen/2;
  \x2 = \startx + 7;
  \x3 = \startx + \beamlen - 0.5;
  \forceyone = 4000;
  \forceytwo = 3000;
  \shearyval1 = 2;
  \shearyval2 = 1.5;
  \momentyval1 = 2;
  \momentyval2 = 1.2;
  \forcezone = 3500;
  \forceztwo = 2500;
  \shearzval1 = 2;
  \shearzval2 = 1;
  \momentzval1 = 1.8;
  \momentzval2 = 1;
}

\begin{tikzpicture}[x=0.25in, y=0.25in, background rectangle/.style={fill=cyan!10}, show background rectangle]
    
    % === FORCE DIAGRAM - Y COLUMN ===
    \draw[thick, fill=white] (\startx,\shafty) rectangle (\startx+\beamlen,\shafty+1);
    \draw[dash pattern=on 2pt off 3pt on 8pt off 3pt] (\startx - 0.5, \shafty + 0.5) -- (\startx + \beamlen + 0.5, \shafty + 0.5) node [right] {$x$};
    \draw (\x0, \shafty + 1.125) -- (\x0, \shafty + 3) node [above] {$y$};

    % Left support
    \draw (\startx, \shafty) -- (\startx+1, \shafty+1);
    \draw (\startx, \shafty+1) -- (\startx+1, \shafty);
    \draw (\startx+1, \shafty) -- (\startx+1, \shafty+1);

    % Right support
    \draw (\startx+\beamlen-1, \shafty) -- (\startx+\beamlen, \shafty+1);
    \draw (\startx+\beamlen-1, \shafty+1) -- (\startx+\beamlen, \shafty);
    \draw (\startx+\beamlen-1, \shafty) -- (\startx+\beamlen-1, \shafty+1);

    % Reactions
    \draw[ultra thick, stealth-] (\x0, \shafty+1) -- (\x0, \shafty+2.5) node[right] {$R_{y}$};
    \draw[ultra thick, stealth-] (\x3, \shafty+1) -- (\x3, \shafty+2.5) node[right] {$R_{y}$};

    % Loads
    \draw[ultra thick, stealth-] (\x1, \shafty) -- (\x1, \shafty-1.5) node[below] {$W_{56}^r$};

    % % Dimensions
    % \draw[thick, stealth-stealth] (\x0 + 1/36, \shafty-0.5) -- (\x1 - 1/36, \shafty-0.5) node [midway, fill=cyan!10] {1};
    % \draw (\x1, \shafty - 0.625) -- (\x1, \shafty - 0.125);

    % \draw[thick, stealth-stealth] (\x0 + 1/36, \shafty - 1.0) -- (\x2 - 1/36, \shafty - 1.0) node [midway, fill=cyan!10] {2};
    % \draw (\x2, \shafty - 1.125) -- (\x2, \shafty - 0.125);

    % \draw[thick, stealth-stealth] (\x0 + 1/36, \shafty - 1.5) -- (\x3 - 1/36, \shafty - 1.5) node [midway, fill=cyan!10] {3};

    % === SHEAR - Y ===
    \draw (\x0, \sheary) node [left] {$O$} -- (\x0 + \beamlen, \sheary) node [right] {$x$};
    \draw (\x0, \sheary+2.5) node [left] {$V_{xz} (\unit{lbf})$} -- (\x0, \sheary-2.5);
    \draw[fill=white] (\x0, \sheary) rectangle (\x1, \sheary-\shearyval1);
    \draw[fill=white] (\x1, \sheary) rectangle (\x3, \sheary+\shearyval1);
    \draw[very thick] 
        (\x0, \sheary) -- 
        (\x0, \sheary-\shearyval1) -- 
        (\x1, \sheary-\shearyval1) node[midway, below] {$-2161$} -- 
        (\x1, \sheary+\shearyval1) -- 
        (\x3, \sheary+\shearyval1) node[midway, above] {$2161$} -- 
        (\x3, \sheary);

    % === MOMENT - Y ===
    \fill[white] (\x0, \momenty) -- 
        (\x1, \momenty-\momentyval1) -- 
        (\x3, \momenty) -- cycle;
    \draw (\x0, \momenty) node [left] {$O$} -- (\x0 + \beamlen, \momenty) node [right] {$x$};
    \draw (\x0, \momenty+2.5) node [align=center, left] {$M_{xz}$\\$(\unit{lbf\cdot in})$} -- (\x0, \momenty-2.5);
    \draw[very thick] 
        (\x0, \momenty) -- 
        (\x1, \momenty-\momentyval1) node [below] {$-5403$} -- 
        (\x3, \momenty);

    % === TORSION ===
    \fill[fill=white] (\x1, \torquey) rectangle (\x3, \torquey+\shearyval1);

    \draw (\x0, \torquey) node [left] {$O$} -- (\x0 + \beamlen, \torquey) node [right] {$x$};
    \draw (\x0, \torquey+2.5) node [align=center, left] {$T$\\$(\unit{lbf\cdot in})$} -- (\x0, \torquey);
    \draw[very thick] 
        (\x0, \torquey) -- 
        (\x1, \torquey) --
        (\x1, \torquey+\shearyval1);
    \draw[very thick, ->] (\x1, \torquey+\shearyval1) -- 
    (\x3+0.25, \torquey+\shearyval1) node[midway, above] {$65133$};

    % === FORCE DIAGRAM - Z COLUMN ===
    \draw[thick, fill=white] (\startx + \coloff, \shafty) rectangle (\startx + \beamlen + \coloff, \shafty + 1);
    \draw[dash pattern=on 2pt off 3pt on 8pt off 3pt] (\startx - 0.5 + \coloff, \shafty + 0.5) -- (\startx + \beamlen + 0.5 + \coloff, \shafty + 0.5) node [right] {$x$};
    \draw (\x0 + \coloff, \shafty + 1.125) -- (\x0 + \coloff, \shafty + 3) node [above] {$z$};

    % Supports
    \draw (\startx + \coloff, \shafty) -- (\startx + 1 + \coloff, \shafty + 1);
    \draw (\startx + \coloff, \shafty + 1) -- (\startx + 1 + \coloff, \shafty);
    \draw (\startx + 1 + \coloff, \shafty) -- (\startx + 1 + \coloff, \shafty + 1);
    \draw (\startx + \beamlen - 1 + \coloff, \shafty) -- (\startx + \beamlen + \coloff, \shafty + 1);
    \draw (\startx + \beamlen - 1 + \coloff, \shafty + 1) -- (\startx + \beamlen + \coloff, \shafty);
    \draw (\startx + \beamlen - 1 + \coloff, \shafty) -- (\startx + \beamlen - 1 + \coloff, \shafty + 1);

    % Reactions
    \draw[ultra thick, stealth-] (\x0 + \coloff, \shafty) -- (\x0 + \coloff, \shafty-1.5) node[below] {$R_{z}$};
    \draw[ultra thick, stealth-] (\x3 + \coloff, \shafty) -- (\x3 + \coloff, \shafty-1.5) node[below] {$R_{z}$};

    % Loads
    \draw[ultra thick, stealth-] (\x1 + \coloff, \shafty+1) -- (\x1 + \coloff, \shafty+2.5) node[above] {$W^t_{56}$};

    % % Dimensions - Z column
    % \draw[thick, stealth-stealth] (\x0 + \coloff + 1/36, \shafty - 0.5) -- (\x1 + \coloff - 1/36, \shafty - 0.5) node [midway, fill=cyan!10] {1};
    % \draw (\x1 + \coloff, \shafty - 0.625) -- (\x1 + \coloff, \shafty - 0.125);

    % \draw[thick, stealth-stealth] (\x0 + \coloff + 1/36, \shafty - 1.0) -- (\x2 + \coloff - 1/36, \shafty - 1.0) node [midway, fill=cyan!10] {2};
    % \draw (\x2 + \coloff, \shafty - 1.125) -- (\x2 + \coloff, \shafty - 0.125);

    % \draw[thick, stealth-stealth] (\x0 + \coloff + 1/36, \shafty - 1.5) -- (\x3 + \coloff - 1/36, \shafty - 1.5) node [midway, fill=cyan!10] {3};

    % === SHEAR - Z ===
    \draw (\x0 + \coloff, \sheary) node [left] {$O$} -- (\x0 + \beamlen + \coloff, \sheary) node [right] {$x$};
    \draw (\x0 + \coloff, \sheary+2.5) node [left] {$V_{xy} (\unit{lbf})$} -- (\x0 + \coloff, \sheary - 2.5);
    \draw[fill=white] (\x0 + \coloff, \sheary) rectangle (\x1 + \coloff, \sheary+\shearzval1);
    \draw[fill=white] (\x1 + \coloff, \sheary) rectangle (\x3 + \coloff, \sheary-\shearzval1);
    \draw[very thick]
        (\x0 + \coloff, \sheary) --
        (\x0 + \coloff, \sheary+\shearzval1) --
        (\x1 + \coloff, \sheary+\shearzval1) node[midway, above] {$5142$} --
        (\x1 + \coloff, \sheary-\shearzval1) --
        (\x3 + \coloff, \sheary-\shearzval1) node[midway, below] {$-5142$} --
        (\x3 + \coloff, \sheary);

    % === MOMENT - Z ===
    \fill[white] (\x0 + \coloff, \momenty) --
        (\x1 + \coloff, \momenty+\momentzval1) --
        (\x3 + \coloff, \momenty) -- cycle;
    \draw (\x0 + \coloff, \momenty) node [left] {$O$} -- (\x0 + \beamlen + \coloff, \momenty) node [right] {$x$};
    \draw (\x0 + \coloff, \momenty+2.5) node [align=center, left] {$M_{xy}$\\$(\unit{lbf\cdot in})$} -- (\x0 + \coloff, \momenty);
    \draw[very thick]
        (\x0 + \coloff, \momenty) --
        (\x1 + \coloff, \momenty+\momentzval1) node[above] {$12855$} --
        (\x3 + \coloff, \momenty);

    % === MOMENT - COMB ===
    \fill[white] (\x0 + \coloff, \torquey) --
        (\x1 + \coloff, \torquey+\momentzval1) --
        (\x3 + \coloff, \torquey) -- cycle;
    \draw (\x0 + \coloff, \torquey) node [left] {$O$} -- (\x0 + \beamlen + \coloff, \torquey) node [right] {$x$};
    \draw (\x0 + \coloff, \torquey+2.5) node [align=center, left] {$M_{total}$\\$(\unit{lbf\cdot in})$} -- (\x0 + \coloff, \torquey);
    \draw[very thick]
        (\x0 + \coloff, \torquey) --
        (\x1 + \coloff, \torquey+\momentzval1) node[above] {$13944$} --
        (\x3 + \coloff, \torquey);
\end{tikzpicture}

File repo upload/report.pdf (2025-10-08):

# Gearbox Design Report

Luke McGinnis
Eastern Michigan University ME 330: Machine Design
Dr. Emad Tanbour

April 21, 2025

## Contents

1 Introduction | 2
2 Gears Specifications | 3
3 Shaft Layout | 4
4 Shaft Design | 7
5 Gears | 10
6 Other Components | 11
7 Appendices | 13
A Source Code | 13
B Drawings | 13

1


## 1 Introduction

### 1.1 Project Statement

Using machine design principles, comprehensively design and create a CAD model of a three-stage speed reduction gearbox.

### 1.2 Overall Requirements

- Reduce the shaft speed from an input of 1,750 rpm to an output of 130 ± 5 rpm.
- Tolerate an input power of 135 hp.
- Consist of four shafts, one input, two intermediate, and one output.
- Use helical gears only.
- Be lubricated and sealed.

### 1.3 Design Objectives

- Minimize the total size of the gearbox.
- Ensure the gearbox is easy to assemble and disassemble.
- Ensure manufacturability of all components.

### 1.4 Methods

- Design report will be prepared with LATEX.
- CAD models, assemblies, drawing, simulations, and rendering will be prepared with Solidworks.

2

## 2 Gears Specifications

### 2.1 Requirements

- Overall gear train must convert 1,750 rpm to 130 ± 5 rpm.
- Gear train must handle an input power of 135 hp.
- Gear train must be as compact as possible.
- All gears must be helical.
- Gears must be designed for a service life of 2,000 hours per year and 6 years (12,000 hours total).
- Gears will be lubricated.
- AGMA (American Gear Manufacturers Association) design methodology will be used.

### 2.2 Design Decisions

- All gears will use a standard pressure angle of 20◦
. This is the most common pressure angle used for gearing and thus tooth cutters will be available for the greatest number of diametral pitches [1].
- All gears will have full-depth teeth.
- All gears will have a helix angle of 30◦
. This will allow for maximum advantage of strength and noise benefits of helical gears.

### 2.3 Gear Ratio

In order to achieve the smallest overall package size, we want our three stage ratios to be as close together as possible. Our requirements allow us to deviate from our target output speed of 130 rpm by as much as 5 rpm. If we assume the ideal case of all stage ratios being equal, we can calculate a target individual stage ratio:

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
2.379
Now we can consider possible ratios that get close enough to this value by limiting the denominator of this ideal ratio, to get the closest simple fraction approximations.

Table 1: Stage Gear Ratios Approximating a Ratio of 13:175

Stage Ratio | Train Value | Output Speed | Output Error
NP : NG | e | ωout (rpm) | ∆ωout (rpm)
37 : 88 | 0.0743 | 130.1 | 0.075
29 : 69 | 0.0742 | 129.9 | 0.077
21 : 50 | 0.0741 | 129.7 | 0.35
8 : 19 | 0.0746 | 130.6 | 0.63
5 : 12 | 0.0723 | 126.6 | 3.4
3 : 7 | 0.0787 | 137.8 | 7.8
2 : 5 | 0.0640 | 112.0 | 18

See Appendix A for generation source code used to generate this data.

From Table 1, we see that we have five ratios to choose from that will produce a output speed within 5 rpm of our target output speed of 130 rpm. We will choose a stage ratio of 8 : 19 to get very close to the target speed, and allow for scaling the ratio if we need to change our diametral pitch. Starting by doubling the values to 16 : 38 and testing for meshing interference:
| | 3

NG, max =

N²
P

sin²
(ϕt) − 4k

2

cos²
(ψ)
4k cos(ψ) − 2NP sin²
(ϕt)

=

16²

sin²
(20◦
) − 4(1) cos²

(30◦
)
4 cos(30◦) − 2(16) sin²
(20◦)
= −26.45 | (13-23) [1]

This means that there is no gear size of this specification that would interfere with a pinion of 16 teeth, so we know there will not be any interference in the gear train. We can now obtain our values for torque and speed:

Table 2: Transmission Values by Shaft

Input | Intermediate | Output
Shaft | A | B | C | D
Speed (rpm) | 1750 | 736.8 | 310.2 | 130.6
Torque (lbf · ft) | 405.2 | 962.3 | 2285 | 5428
Pinion Tooth Count | 16 | 16 | 16 | –
Gear Tooth Count | – | 38 | 38 | 38

For now, we can now proceed with tooth counts:

NP
NG
| = N1
| N2 =

N3
N4
| | = N5
| | N6

=

16
38

### 2.4 Estimation of Diametrical Pitch

In order to reduce iteration, we will try to get a preliminary estimations of a diametrical pitch for our gears. To do so, we will analyze the likely critical gear in our gearbox, which is #5, (pinion of shaft C) as it is the pinion with the highest torque.
We will use equation 14-8 and rewrite it in terms of diametrical pitch P:

σ =

| KvPWt
| FY | =⇒ P =

FY σ
| | KvWt

(14-8) [1]

We can simplify the gear to a spur gear, and use the following assumptions [1]:

F : The face width is recommended to be 3p to 5p.

Y : The Lewis form factor ranges from 0.24 to 0.485.

σ : Endurance strength of steel gears range from 22 ksi to 75 ksi.

Kv : The velocity factor is a function of pitch-line velocity V , which is dependent on P. The velocity factor ranges

from 600+V

600 to q

78+√
V
78 .

We can now rewrite all variables as constants or in terms of P using pP = π, r =

N
2P
| | | | , V = ωr, and Wt = 135 hp/V .
After solving numerically, we can obtain a very conservative value of P of 1.891 teeth/in, and a nonconservative value of 5.338 teeth/in. For now, we will choose from tooth sizes in general use [1], and select Pt = 3 teeth/in.

## 3 Shaft Layout

Our next step is specify the general layout of the shafts and axial locations of gears and bearings. In additon, we will address attaching components to shafts.

4

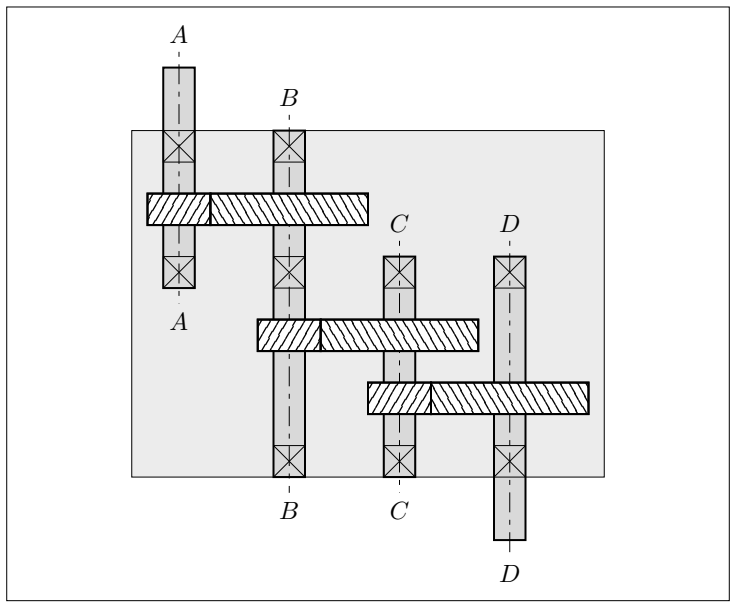
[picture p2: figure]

Figure 1: First Iteration of General Gearbox Shaft Layout

### 3.1 Requirements

- There must be 4 shafts: one input, two intermediate, and one output.
- Gearbox size must be minimized.
- Shafts should be as short as possible.
- Input and output shafts must extend outside of the gearbox housing by two times their diameter.
- Where possible, shaft diameters should be standard sizes.
- Shafts geometry should include means for rotating components to be affixed, such as keyways and retaining rings.

### 3.2 Decisions

- In order to transmit torque via shafts, keyways will be used.
- Because helical gears will have a great axial force on one side, and little to no force on the other, a mix of shoulders and retaining rings will be used.
- Shoulders will be used to hold shafts in place on bearings.

### 3.3 General Layout

Based on these requirements and design decisions I designed a first iteration of the shaft layout. My layout uses three planes of bearings and three planes of gears to eliminate interference between gears. In this layout, shaft B is the longest shaft, but is supported by three bearings, reducing the effective length. This layout has one pair of gears above the middle bearing plane, and two pairs below. I believe this is a flaw with this design: this causes shafts C and D to have to be longer to accommodate the additonal gears and clearance. As shaft C or D are likely critical due to the high torque on them, it is wise to adjust this design to reduce the length of these shafts.
5

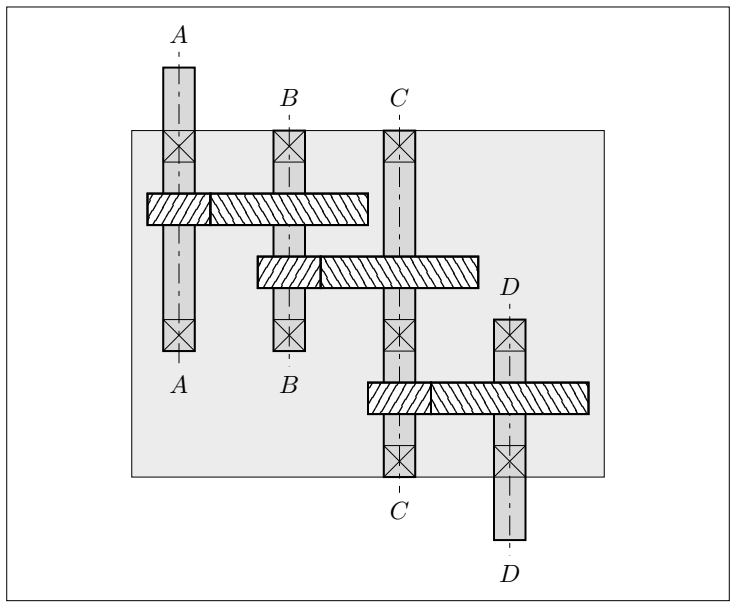
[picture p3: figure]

Figure 2: Final General Gearbox Shaft Layout

I modified the layout to move an additional pair of gears above the middle plane of bearings. This allowed me to reduce the length of shafts C and D by increasing the lengths of A and B. This is reasonable, because it reduces the stress of the most critical shafts, reducing the required diameter. Shaft C is now the longest shaft, but again, the middle bearing significantly decreases the effective length.

### 3.4 Dimensions

From the general layout, axial dimensions now have to be specified. Each shaft’s length is a combination of the following lengths:

F Face Width for helcial gears is recommended to be at least two times the axial pitch. Using formula (13-17)[1], px = pt/2 · tan(ψ) = 2 · π/3/ tan(30◦
) = 1.81. Increase to 2 in and revisit if needed.

S : The axial length of the shoulder around the gear is determed by proportionality to the shaft minor diameter and shoulder diameter. This length will also accommodate the retaining hardware on the side of each gear opposite the axial force and shoulder. To meet both requirements, choose 1 in.

B : The axial length of the bearing is determined by the shortest bearing able to support the required load of each shaft. Estimate to be 1 in.

E : The external length of the input and output shafts from the gearbox housing. Per design requirements this must be double the diameter of the external shaft. As diameters are currently unknown, estimate to be 2.5 in. This dimension will later accommodate shaft seals and likely need to be increased. but this portion of the shafts will just be under torsion and will not be critical, and therefore changes in E will likely be inconsequential for stress life.

### 3.5 Force Analysis

Now that gear diameters and axial dimension are known we can produce free-body diagrams, shear-moment diagrams, and obtain maximum bending moments for each shaft.

6

## 4 Shaft Design

### 4.1 Decisions

- Since all shafts must be designed for an infinite life, all shafts will be made of steel.
- To reduce costs and manufacturing difficulty, all shafts will be made of a single material.

### 4.2 Force Analysis

Due to the speed of the gearbox decreasing and the torque increasing, shaft C or D are the critical shaft. I will conduct a force analysis on both to find the most critical point.
Shaft C:

V34 =

ωCN4
P

= 1,029 ft/min

Wt
34 = P/V34 = 4,330 lbf
Wr

34 = Wt
34 tan(ϕt) = 1,820 lbf
Wx

34 = Wt
34 tan(ψ) = 2,500 lbf

V56 =

ωCN5
P

= 433 ft/min

Wt
56 = P/V56 = 10,284 lbf
Wr

56 = Wt
56 tan(ϕt) = −4,322 lbf
Wx

56 = Wt
56 tan(ψ) = −5,937 lbf

Shaft C has three bearings, two gears. Split shaft into two portions, left and right and evaluate independently. The middle bearing will support the loads on both sides.

Ray = −Wr
34

B/2 + S + F/2

lleft

= −569 lbf

Rby = −Wr
34

B/2 + 2S +
3/2 F

lleft

−

1
2

Wr
56 = 910 lbf

Rcy = −

1
2

Wr
56 = 2,161 lbf

Raz = −Wt
34

B/2 + S + F/2

lleft

= −1,351 lbf

Rbz = −Wt
34

B/2 + 2S +
3/2 F

lleft

−

1
2

Wt
56 = −8,119 lbf

Rcz =

1
2

Wt
56 = −5,142 lbf

Rbx = −3,438 lbf T =

Wt
56N5
2P

= 27,424 lbf · in

Shaft D:

Wt
56 = P/V56 = −9,331 lbf
Wr

56 = Wt
56 tan(ϕt) = −3,921 lbf
Wx

56 = Wt
56 tan(ψ) = −5,386 lbf

Ry = −

1
2

Wr
56 = 1,960 lbf

Rz = −

1
2

Wt
56 = 4,665 lbf

T =

Wt
56N6
2P

= 65,133 lbf · in

### 4.3 Stress Analysis

Shafts C and D are both critical at the point of the meshing pair gears 5 and 6. Both shafts have the same bending moment at that point, but shaft D has a far higher torque. Therefore the axial location of gear 6 on shaft D is critical. First choose inexpensive 1020 CD Steel. Calculate endurance limit based off of 90% reliability and a estimated 2 in diameter:

Se = kakbkeS

′
e = 0.80 · 0.82 · 0.90 · 0.5 · 68 ksi = 19.9 ksi | (6-17) [1]

7

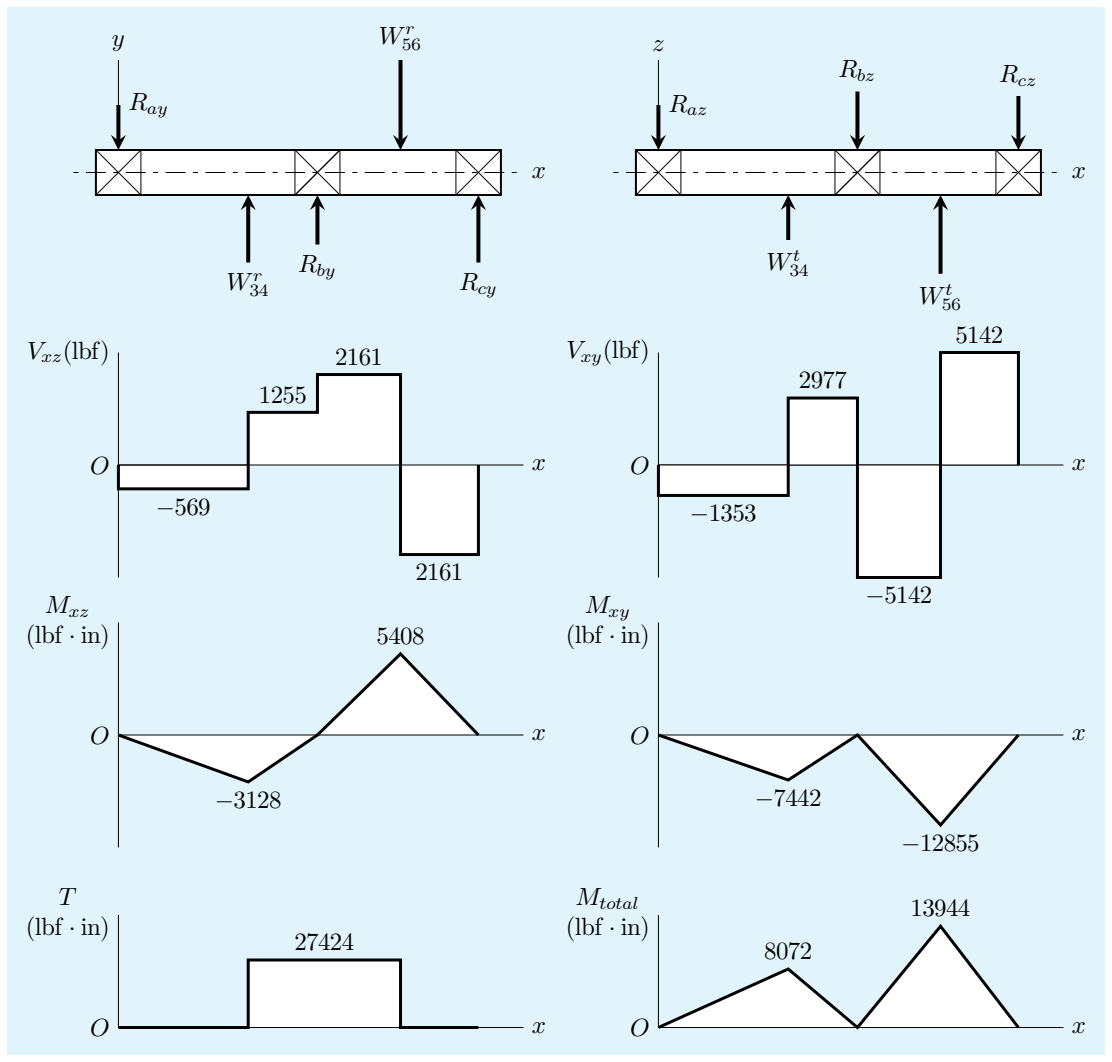
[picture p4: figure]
Ray; Rby W; Rcy; Vxz(lbf); Mxz (lbf · in); (lbf · in); Raz; Rbz; Rcz; Vxy(lbf); Mxy (lbf · in); Mtotal (lbf · in)

Figure 3: Force Analysis of Shaft C

Using the DE-Goodman criteria, find the critical diameter for shaft D. This location will have an end-milled keyway to transmit motion between gears, so calculate fatigue notch factors [1]:

r = 0.02 · 2 in = 0.04 in =⇒ q = 0.65, qs = 0.7 Kf = 1 + q (Kt − 1) = 1 + 0.65(2.14 − 1) = 1.74 Kfs = 1 + qs(Kts − 1) = 1 + 0.7(3.0 − 1) = 2.4

For a constantly rotating shaft, Ta = Mm = 0 and use values from force analysis for Tm and Ma. Also use n = 1.25 for a factor of safety.

8

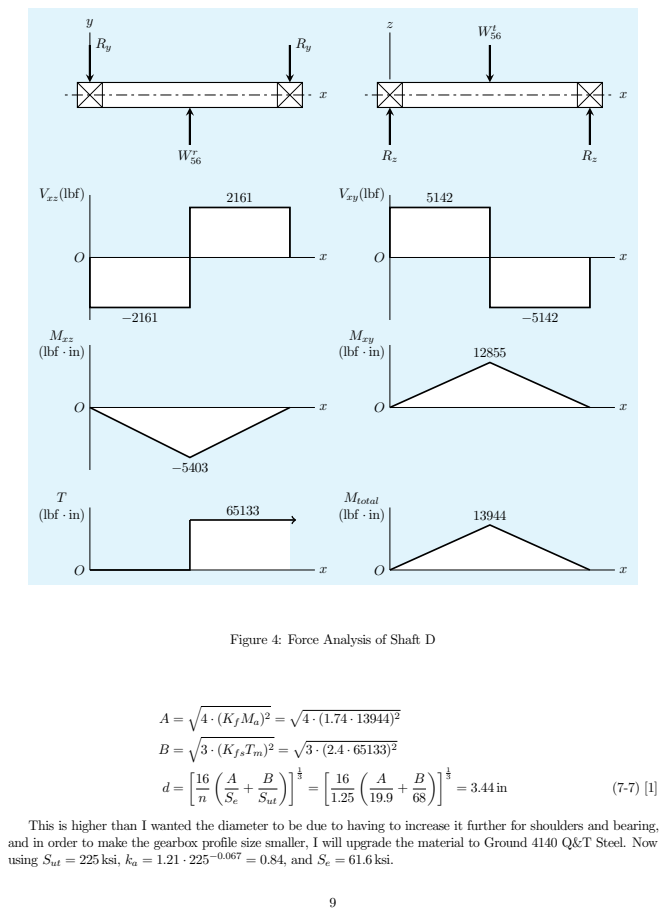
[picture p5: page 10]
Vxz(lbf); Mxz (lbf · in); (lbf · in); Vxy(lbf); Mxy; Mtotal; q 4 · (KfMa); q 3 · (KfsTm); Sut  1 3

Figure 4: Force Analysis of Shaft D

This is higher than I wanted the diameter to be due to having to increase it further for shoulders and bearing,
and in order to make the gearbox profile size smaller, I will upgrade the material to Ground 4140 Q&T Steel. Now
using Sut = 225 ksi, ka = 1.21 · 225⁻⁰.067 = 0.84, and Se = 61.6 ksi.

d =

16

1.25
A
61.6

+

B

225 1
3
= 2.33 in

Increase this to 2.5 in. This diameter will be the minimum diameter of all shafts in the gearbox. Next check first cycle yielding by checking critical point of shaft D:

σ

′
max =

"
32KfMa
πd³

2
+ 3
16KfsTm
πd³

# 1

2

=

"
32 · 2.4 · 13944
π · 2.5

3

2
+ 3
16 · 2.4 · 65133
π · 2.5

3

# 1

2

= 112.3 ksi

ny =

Sy
σ

′
max

=

208
90.9

= 2.29

Next check sensitive points for deflection and slope. One option would be to use beam deflection equations, but I chose to use the derivative relationship between bending moment, slope, and deflection:

θ(x) = 1

EI Z
Mdx

y(x) = Z
θ(x) = 1

EI Z Z Mdxdx

E = 30,000 ksi I =

π(2.5 in)⁴
64

Table 3: Slope and Deflection Values along Shaft C

Point of Interest | Position | Slope | Deflection
| x (in) | θ rad | y (in)
Left Bearing | 0.5 | 0.0000032 | 0.00000053
Gear 4 | 5.5 | 0.00039 | 0.00071
Middle Bearing | 8 | 0.00056 | 0.0020
Gear 5 | 10.5 | 0.00086 | 0.0036
Right Bearing | 13 | 0.0012 | 0.0063

All bearings and gears are within the required limits, although the right bearing slope is just barley within limits[1]. Consider during bearing selection.

## 5 Gears

Continuing with perviously used specification for gears and loading, I now need to fully specify gears. Since gear 5 is the smallest gear transmitting the largest load, it will be critical.
Gear 5 Wear:

10

I =

cosϕt sinϕtmG
2mN(mG − 1) =

cos (22.80◦

) sin (22.80◦
)

38
16
2 · 1(³⁸
16 − 1) | = 0.31

Qv = 7, B = 0.731, A = 65.1

Kv =

A +

√
V5
A

B
= 1.22

Km = 1.21
Cp = 2300
Ko = Ks = Cf = 1

σc = Cp

s
WtKoKvKs

KmCf
dpF I

= 148,446 psi

For life factor ZN get number of cycles for specified life of 12,000 hours.

L4 = 12,000 hours · 310 rpm = 2.23 × 10⁸ | rev

ZN = 0.95, KR = KT = CH = 1, SH = 1.1

Sc =

SHσc
ZN

=

1.1 · 148446
0.95

= 171,885 psi

Select grade 2 carburized and hardened steel with Sc = 225,000 psi. nc = 225000 · 0.9/197928 = 1.18. Gear 5 Bending:

J = 0.40, KB = 1

σ = WtKv

PdKm
F J

= 51,654 psi

YN = 0.95
σallow = StYN = 58,500 psi

n =

58500
51654

= 1.13

## 6 Other Components

### 6.1 Bearings

Tapered roller bearings must be used to allow for axial loads due to the helical gears. These bearings should be able to be housed by the gearbox casting. The greatest axial force is from gear 6 pushing onto the outer bearing of shaft D at 5,938 lbf. The greatest radial force is on both bearings of shaft D with a value of 2,161 lbf. This is a combined load of 6,318 lbf.
Using the supplier SXF’s catalog to find bearings with a bore diameter of 2.5 in, and with load limits above those required, I selected part number 39585/39520 [2]. This bearing is also compatible with the required speeds, cycles, and mounting requirements. Additionally, bearing 663/653 will be used for the center of shaft C in order to accommodate a larger shaft diameter.

### 6.2 Lubrication

For helical gears with continuous duty and pitch line velocity over 1,000 ft/min, select AGMA 6 EP.

11

### 6.3 Keys

Standard 0.5 in square keys will be used. Using same 4140 Q&T Steel, check for failure by crushing:

F =

T
r

=

65133
2.5

= 26,053 lbf

l =

2Fn
tSy

=

2 · 26053 · n
0.5 · 225000

= 0.93 in1 in

### 6.4 Other Considerations

- Gearbox housing
- Gearbox mounting
- Lubrication
- Sealing
- Maintenance/Inspection Schedule
- FMEA

12

## 7 Appendices

## Appendix A Source Code

Script Used to Generate Possible Gear Ratios (approximate gear ratio.py)

1 """Generates possible intermediate gear ratios.

2
3 | Ratios are based on an specified overall ratio, a maximum tooth count and a
4 | number of stages. Generates stage ratios where all stages are identical to
5 | minimize total package size.
6 | """

7
8 | from fractions import Fraction
9 | import pandas as pd

10
11 | input_speed = 1750 # rpm
12 | target_output_speed = 130 # rpm
13 | number_of_stages = 3
14 | maximum_tooth_count = 150

15
16 | target_ratio = Fraction(target_output_speed, input_speed)
17 | target_stage_ratio = Fraction(target_ratio ** (1/number_of_stages))

18
19 | ratios = []
20 | max_denominator = maximum_tooth_count

21
22 | # Iteratively reduce denominator until all close ratios are found.
23 | while max_denominator > 1:
24 | stage_ratio = target_stage_ratio.limit_denominator(max_denominator)
25 | ratios.append(stage_ratio)
26 | max_denominator = stage_ratio.denominator - 1

27
28 | # Store data in Dataframe.
29 | df = pd.DataFrame({"Stage Ratio": ratios})
30 | df["Overall Train Value"] = df["Stage Ratio"].astype(float) ** 3
31 | df["Output Speed (rpm)"] = df["Overall Train Value"] * input_speed
32 | df["Output Speed Error (rpm)"] = (df["Output Speed (rpm)"] - target_output_speed).abs()
Appendix B | Drawings

13

B | B

2

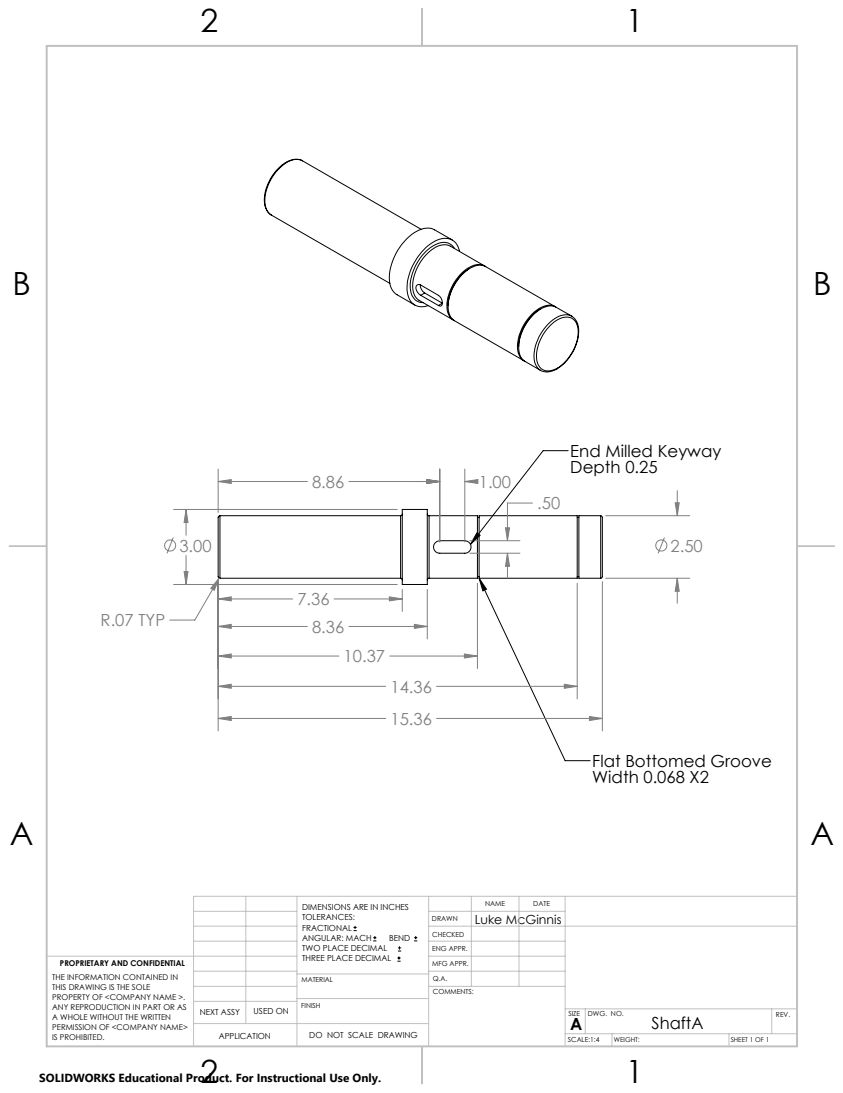
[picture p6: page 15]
R.07 TYP; End Milled Keyway Depth 0.25; COMMENTS:

Flat Bottomed Groove
Width 0.068 X2

TOLERANCES: FRACTIONAL ANGULAR: MACH BEND TWO PLACE DECIMAL THREE PLACE DECIMAL | | NAME | DATE DIMENSIONS ARE IN INCHES

DRAWN | Luke McGinnis

CHECKED
ENG APPR.

PROPRIETARY AND CONFIDENTIAL THE INFORMATION CONTAINED IN THIS DRAWING IS THE SOLE PROPERTY OF <COMPANY NAME >. ANY REPRODUCTION IN PART OR AS A WHOLE WITHOUT THE WRITTEN PERMISSION OF <COMPANY NAME> IS PROHIBITED. | | | MFG APPR.

MATERIAL | Q.A.

NEXT ASSY | USED ON | FINISH

SIZE A | DWG. NO. ShaftA | REV.

APPLICATION | | DO NOT SCALE DRAWING

SCALE:1:4 | WEIGHT: | SHEET 1 OF 1

SOLIDWORKS Educational Product. For Instructional Use Only.

B | B

2

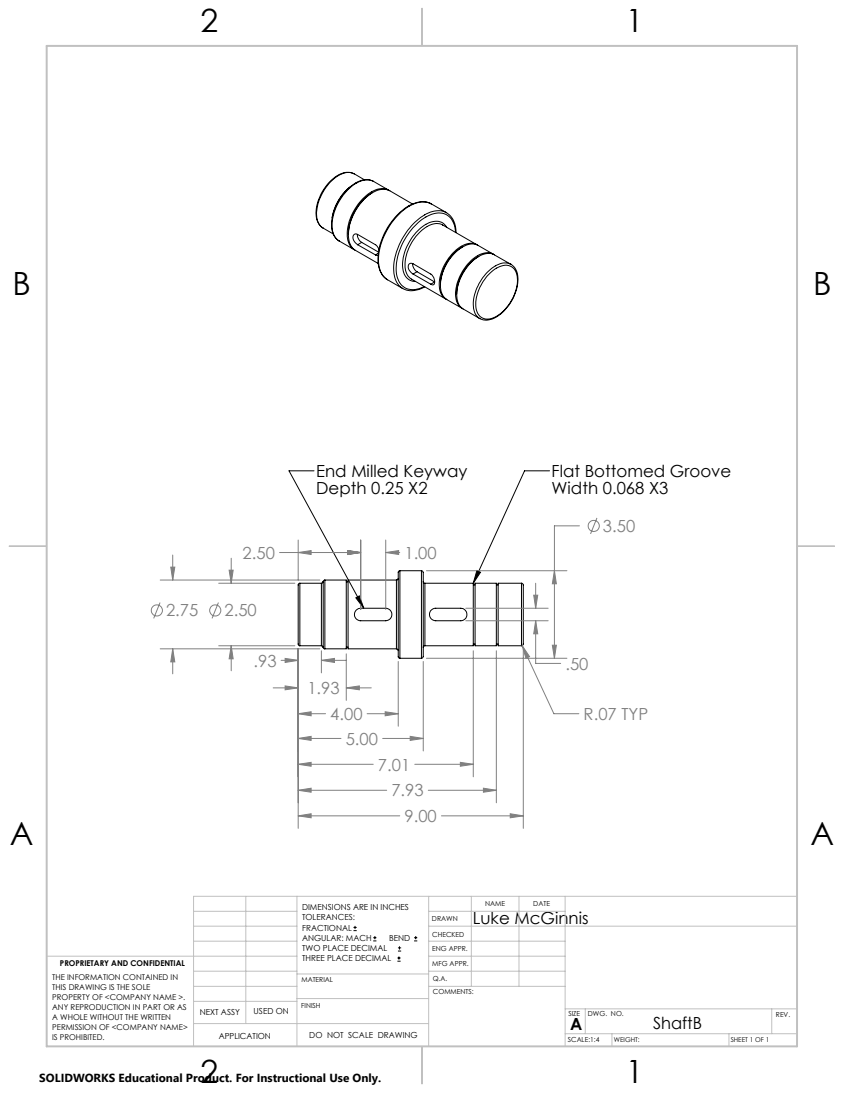
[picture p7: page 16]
R.07 TYP; Flat Bottomed Groove Width 0.068 X3; COMMENTS:

End Milled Keyway
Depth 0.25 X2

TOLERANCES: FRACTIONAL ANGULAR: MACH BEND TWO PLACE DECIMAL THREE PLACE DECIMAL | | NAME | DATE DIMENSIONS ARE IN INCHES

DRAWN | Luke McGinnis

CHECKED
ENG APPR.

PROPRIETARY AND CONFIDENTIAL THE INFORMATION CONTAINED IN THIS DRAWING IS THE SOLE PROPERTY OF <COMPANY NAME >. ANY REPRODUCTION IN PART OR AS A WHOLE WITHOUT THE WRITTEN PERMISSION OF <COMPANY NAME> IS PROHIBITED. | | | MFG APPR.

MATERIAL | Q.A.

NEXT ASSY | USED ON | FINISH

SIZE A | DWG. NO. ShaftB | REV.

APPLICATION | | DO NOT SCALE DRAWING

SCALE:1:4 | WEIGHT: | SHEET 1 OF 1

SOLIDWORKS Educational Product. For Instructional Use Only.

B | B

2

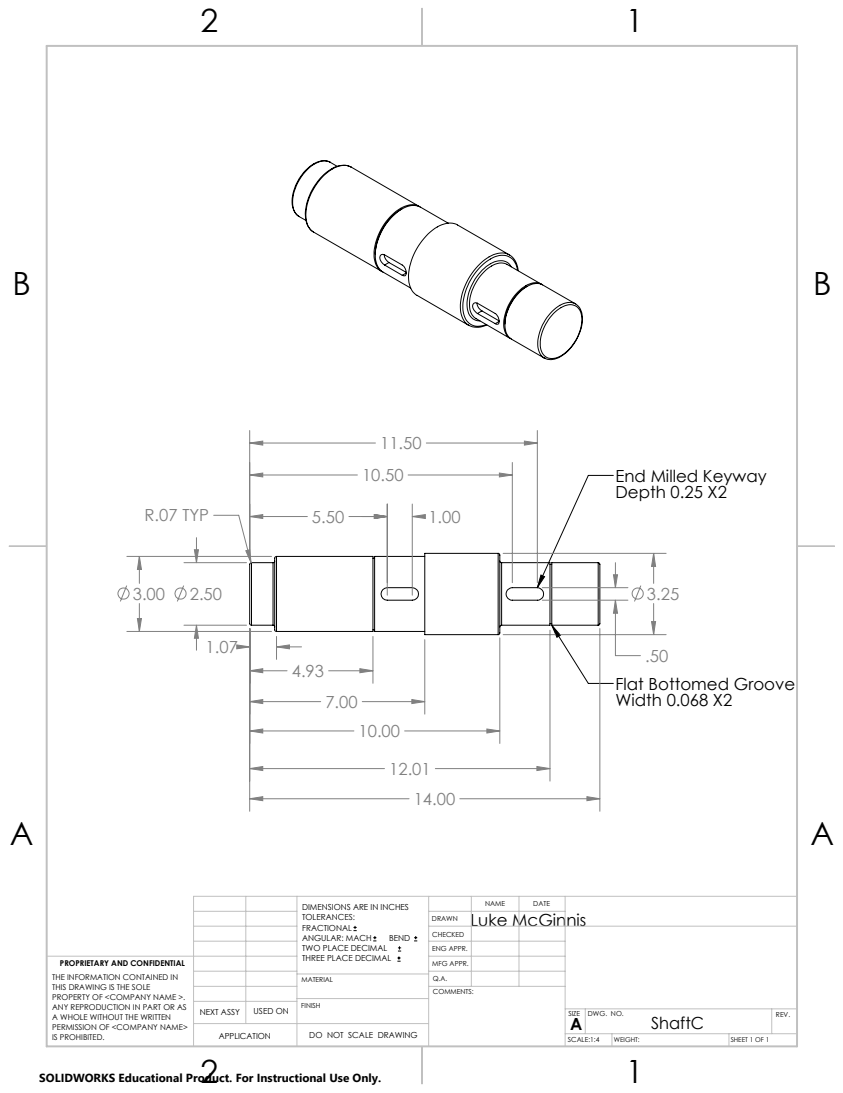
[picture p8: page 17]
R.07 TYP; Flat Bottomed Groove Width 0.068 X2; COMMENTS:

End Milled Keyway
Depth 0.25 X2

TOLERANCES: FRACTIONAL ANGULAR: MACH BEND TWO PLACE DECIMAL THREE PLACE DECIMAL | | NAME | DATE DIMENSIONS ARE IN INCHES

DRAWN | Luke McGinnis

CHECKED
ENG APPR.

PROPRIETARY AND CONFIDENTIAL THE INFORMATION CONTAINED IN THIS DRAWING IS THE SOLE PROPERTY OF <COMPANY NAME >. ANY REPRODUCTION IN PART OR AS A WHOLE WITHOUT THE WRITTEN PERMISSION OF <COMPANY NAME> IS PROHIBITED. | | | MFG APPR.

MATERIAL | Q.A.

NEXT ASSY | USED ON | FINISH

SIZE A | DWG. NO. ShaftC | REV.

APPLICATION | | DO NOT SCALE DRAWING

SCALE:1:4 | WEIGHT: | SHEET 1 OF 1

SOLIDWORKS Educational Product. For Instructional Use Only.

B | B

2

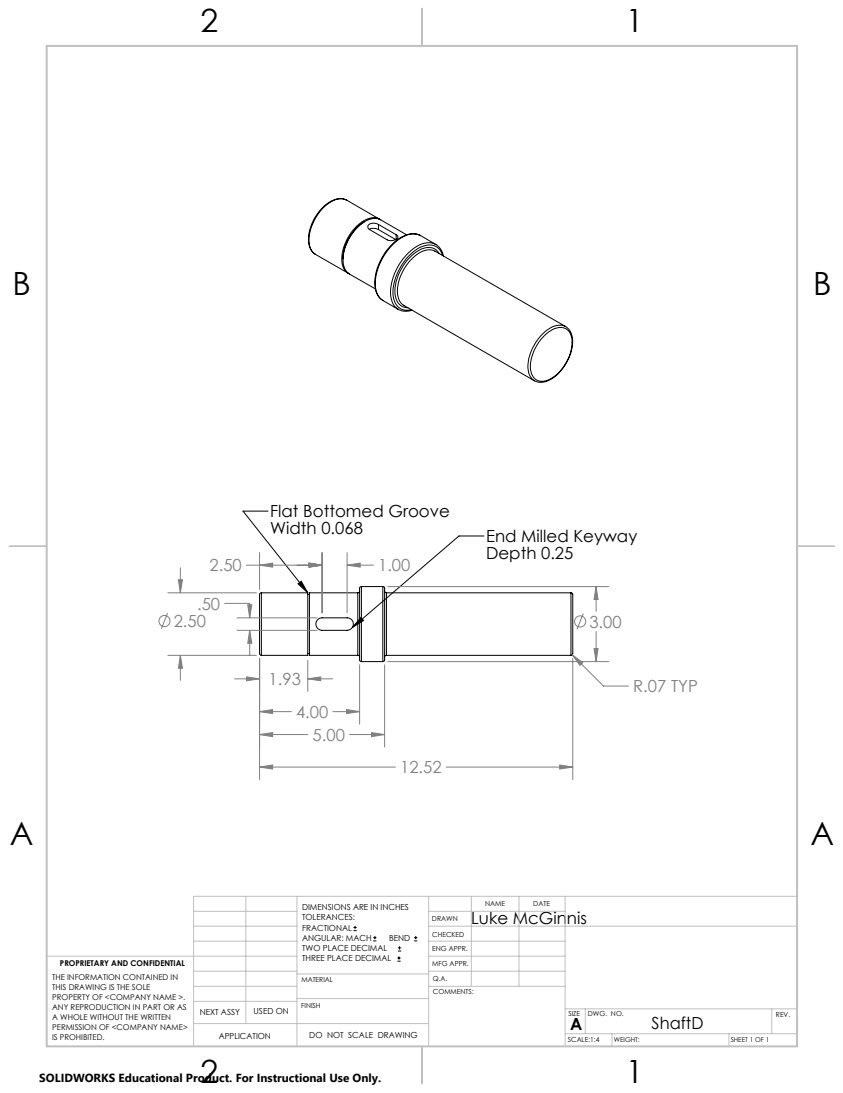
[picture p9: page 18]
R.07 TYP; Width 0.068; End Milled Keyway; Depth 0.25; COMMENTS:

Flat Bottomed Groove

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

DRAWN | Luke McGinnis

CHECKED
ENG APPR.

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

MATERIAL | Q.A.

NEXT ASSY | USED ON | FINISH

SIZE A | DWG. NO. ShaftD | REV.

APPLICATION | | DO NOT SCALE DRAWING

SCALE:1:4 | WEIGHT: | SHEET 1 OF 1

SOLIDWORKS Educational Product. For Instructional Use Only.

## References

[1] Richard G. Budynas and J. Keith Nisbett. Shigley’s Mechanical Engineering Design. 2024 Release. McGraw-Hill, 2024.
[2] SXF. Single row tapered roller bearing. url: https : / / www . skf . com / us / products / rolling -
bearings/roller- bearings/tapered-roller-bearings/single-row- tapered- roller-bearings/productid-39585%2F39520.

18

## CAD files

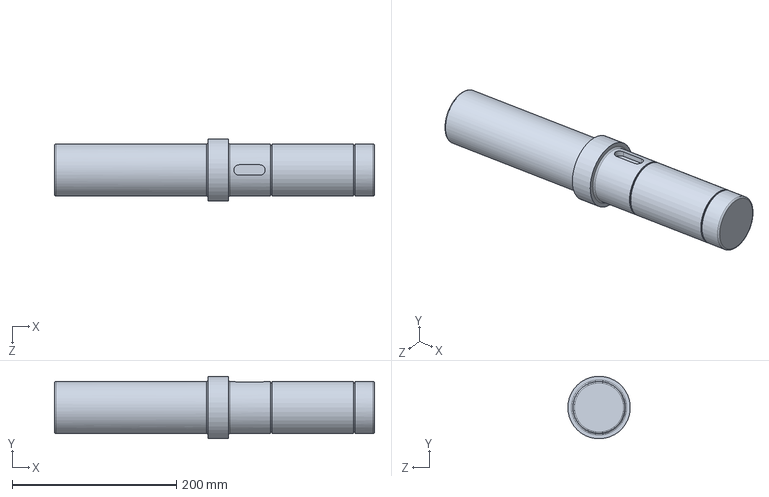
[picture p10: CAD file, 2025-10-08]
repo upload/cad/shafts/ShaftA.SLDPRT
390.1 x 76.1 x 76.1 mm

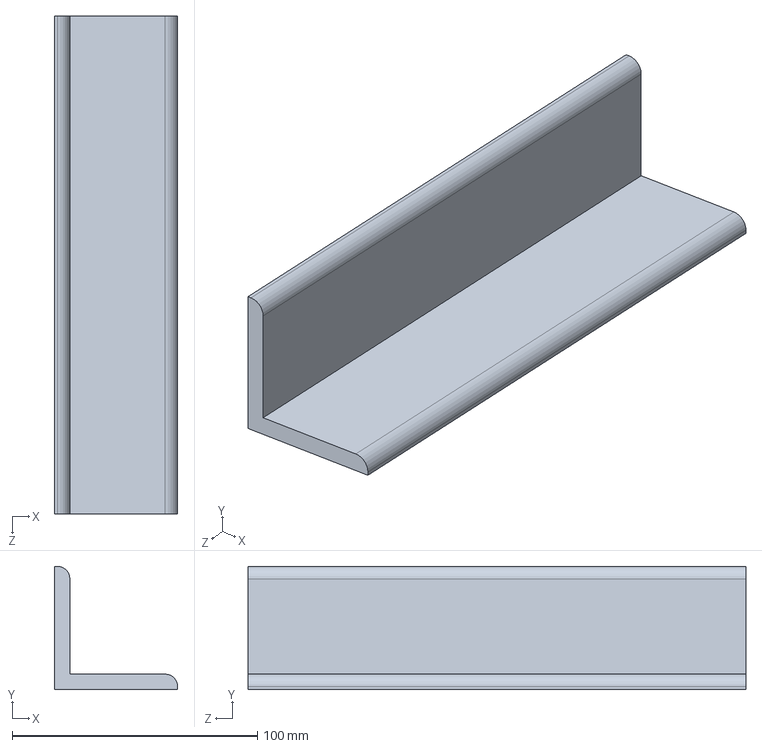
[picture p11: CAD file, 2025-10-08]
repo upload/cad/AngleBracket.SLDPRT
50.3 x 50.3 x 203.2 mm

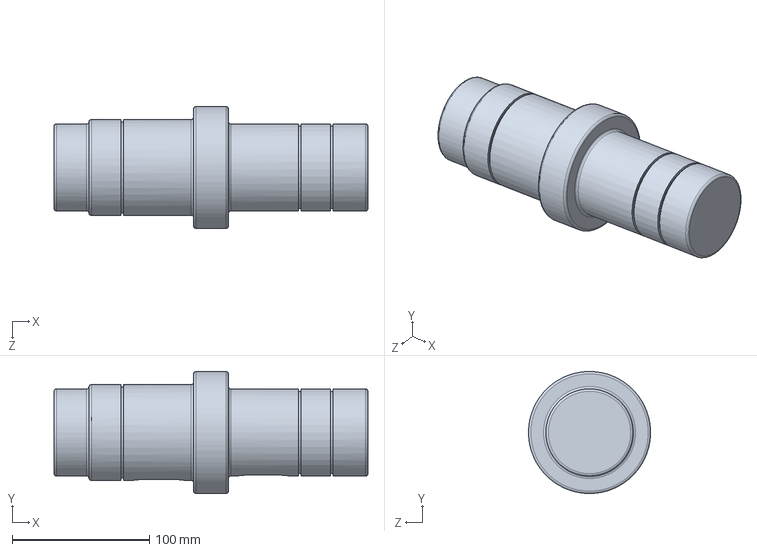
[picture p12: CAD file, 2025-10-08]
repo upload/cad/shafts/ShaftB.SLDPRT
228.6 x 88.9 x 88.8 mm

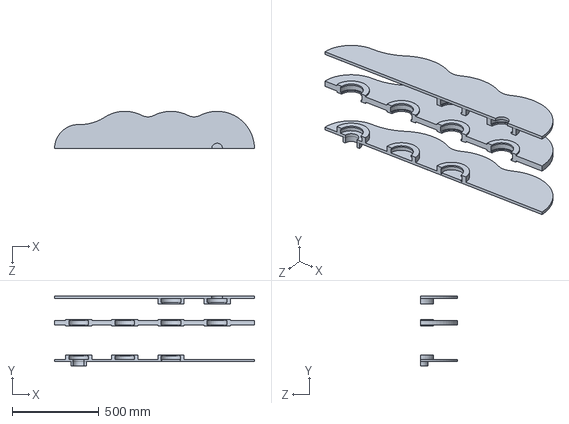
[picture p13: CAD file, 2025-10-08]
repo upload/cad/Housing.SLDPRT
1155.7 x 403.4 x 215.7 mm

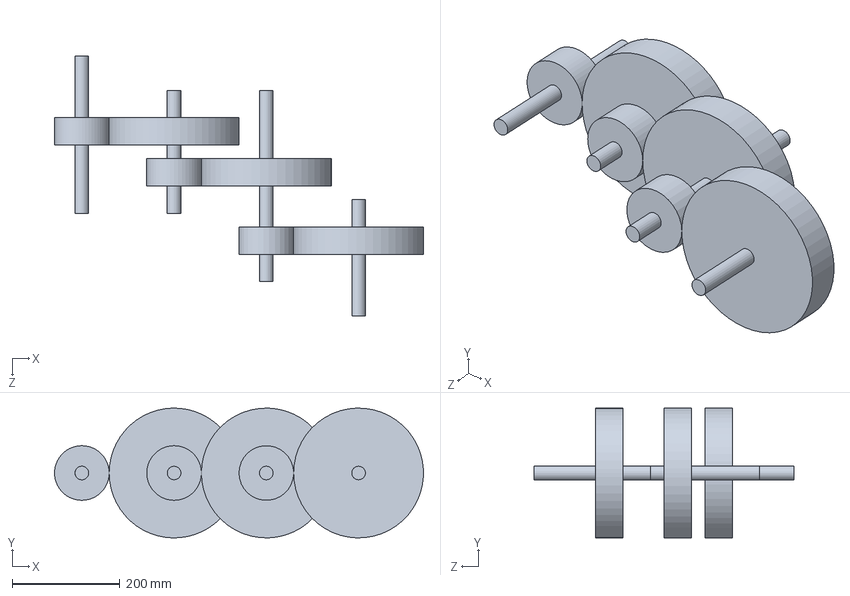
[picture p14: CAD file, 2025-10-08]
repo upload/cad/Layout.SLDPRT
685.8 x 241.2 x 482.6 mm

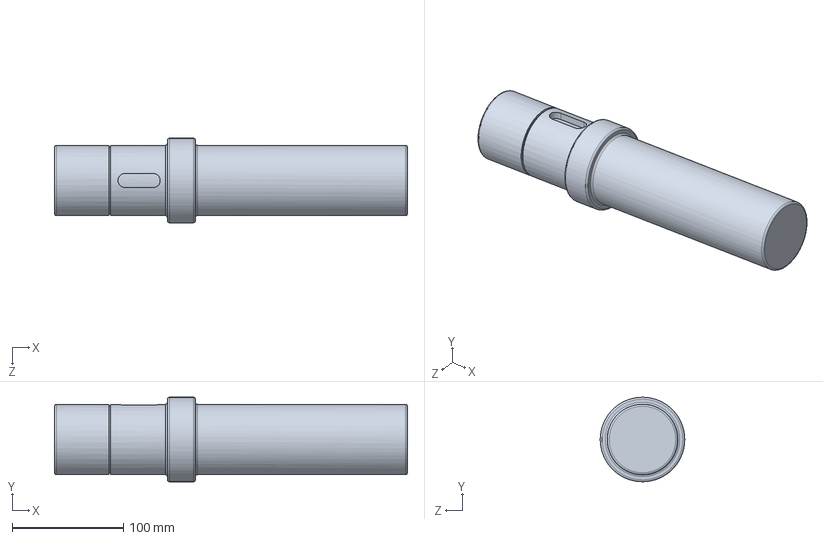
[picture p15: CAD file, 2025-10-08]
repo upload/cad/shafts/ShaftD.SLDPRT
318.0 x 76.2 x 76.2 mm

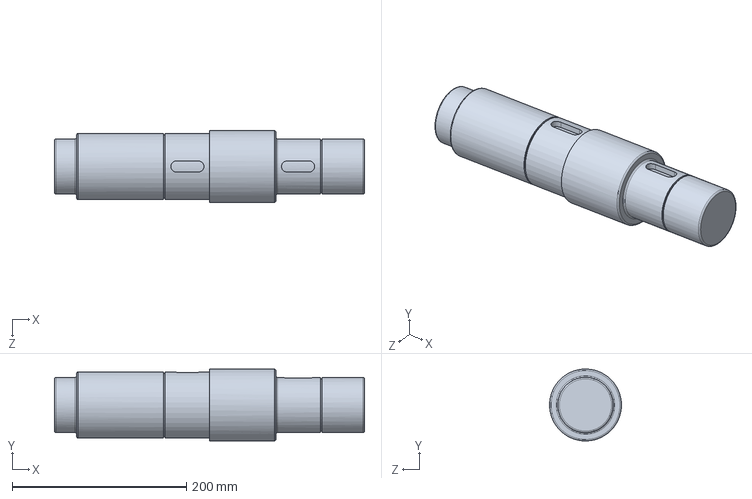
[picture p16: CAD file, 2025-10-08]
repo upload/cad/shafts/ShaftC.SLDPRT
355.6 x 82.5 x 82.5 mm

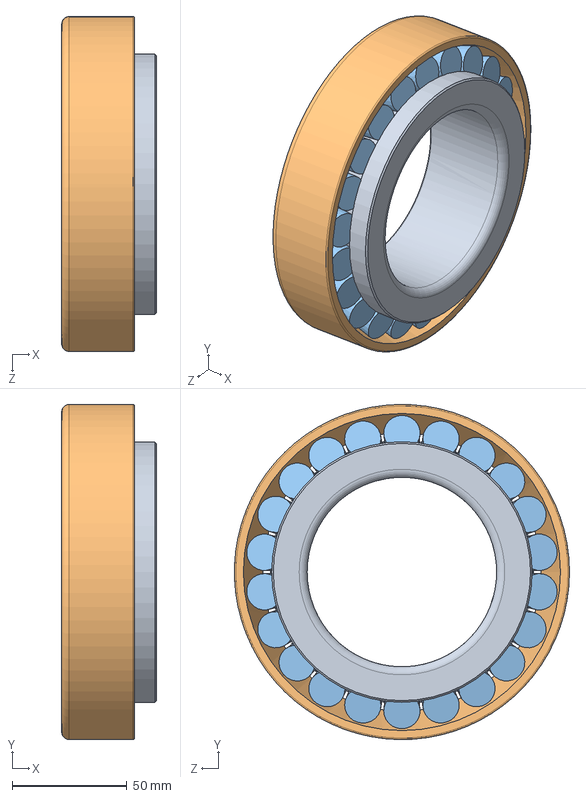
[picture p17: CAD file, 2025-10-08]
repo upload/cad/cots/skf_bearing_663_653_2.SLDASM
41.3 x 146.0 x 146.0 mm
skf_bearing_663_653_2_01
skf_bearing_663_653_2_02
skf_bearing_663_653_2_03

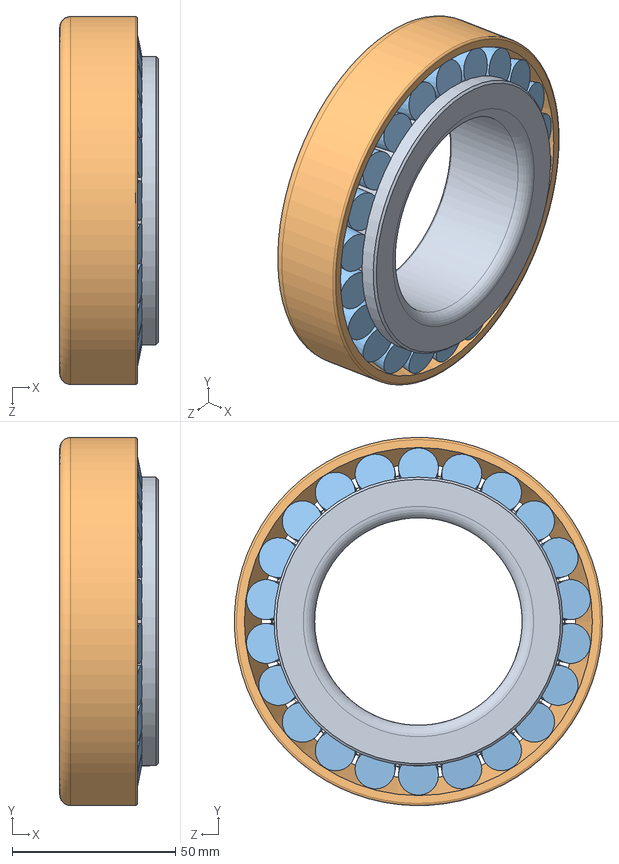
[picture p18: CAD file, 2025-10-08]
repo upload/cad/cots/skf_bearing_39585_39520_2.SLDASM
30.2 x 112.7 x 112.7 mm
skf_bearing_39585_39520_2_01
skf_bearing_39585_39520_2_02
skf_bearing_39585_39520_2_03

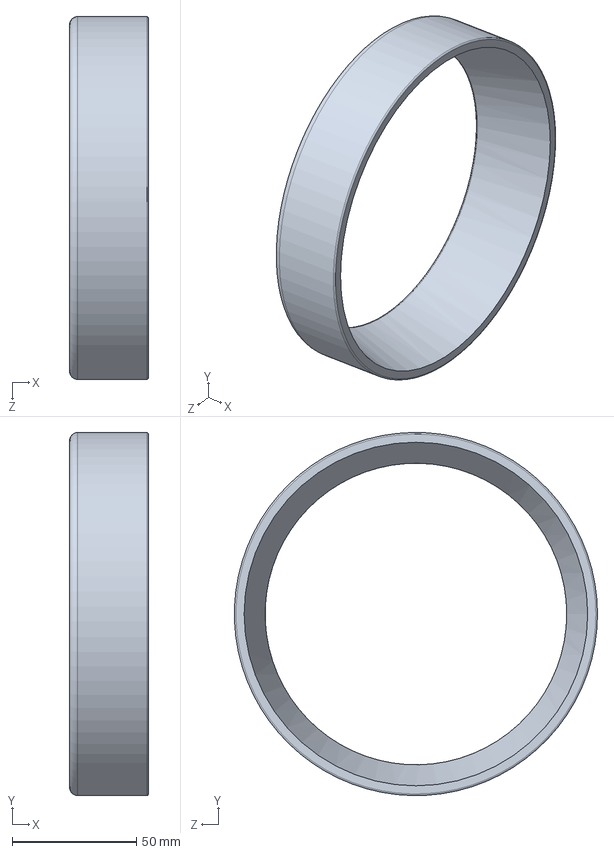
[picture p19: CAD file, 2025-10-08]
repo upload/cad/cots/skf_bearing_663_653_2_02.SLDPRT
31.8 x 146.0 x 146.0 mm

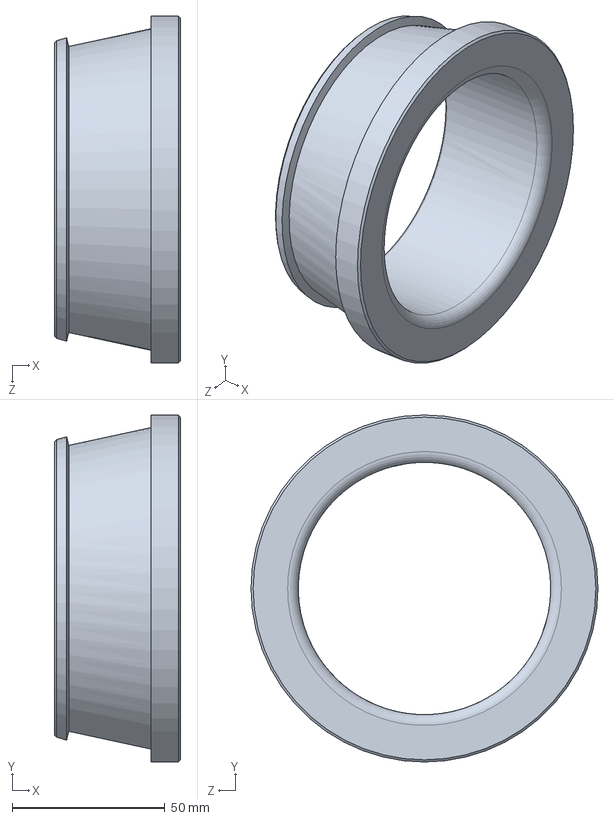
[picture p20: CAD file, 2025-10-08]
repo upload/cad/cots/skf_bearing_663_653_2_01.SLDPRT
41.3 x 113.5 x 113.5 mm

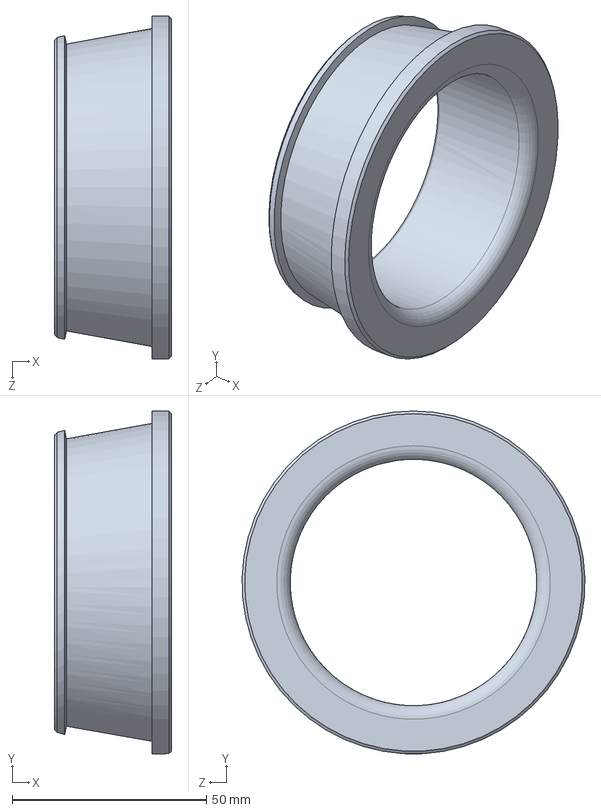
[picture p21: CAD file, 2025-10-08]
repo upload/cad/cots/skf_bearing_39585_39520_2_01.SLDPRT
30.2 x 88.4 x 88.4 mm

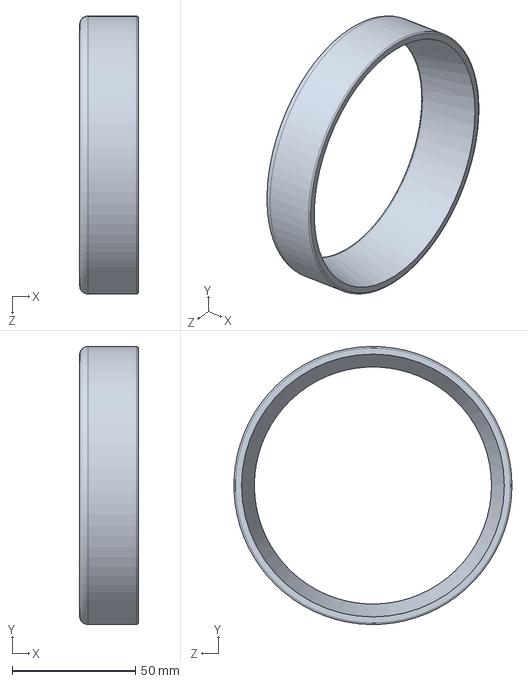
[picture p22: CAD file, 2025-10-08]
repo upload/cad/cots/skf_bearing_39585_39520_2_02.SLDPRT
23.8 x 112.7 x 112.7 mm

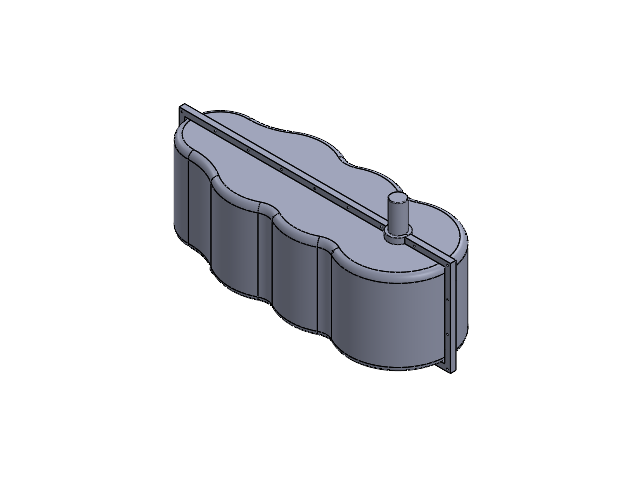
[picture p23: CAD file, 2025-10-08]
repo upload/cad/Gearbox.SLDASM
Housing
ShaftA
helical gear_3_ai x 6
skf_bearing_39585_39520_2_01 x 8
skf_bearing_39585_39520_2_02 x 8
skf_bearing_39585_39520_2_03 x 8
basic external retaining ring_ai x 6
ShaftB
ShaftC
skf_bearing_663_653_2_01
skf_bearing_663_653_2_02
skf_bearing_663_653_2_03
ShaftD

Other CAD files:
repo upload/cad/shafts/ShaftAssemB.SLDASM
repo upload/cad/shafts/ShaftAssemD.SLDASM
repo upload/cad/shafts/ShaftAssemA.SLDASM
repo upload/cad/shafts/ShaftAssemC.SLDASM
repo upload/cad/cots/skf_bearing_39585_39520_2_03.SLDPRT
repo upload/cad/cots/skf_bearing_663_653_2_03.SLDPRT
repo upload/cad/drawings/ShaftA.SLDDRW
repo upload/cad/drawings/ShaftB.SLDDRW
repo upload/cad/drawings/ShaftC.SLDDRW
repo upload/cad/drawings/ShaftD.SLDDRW
